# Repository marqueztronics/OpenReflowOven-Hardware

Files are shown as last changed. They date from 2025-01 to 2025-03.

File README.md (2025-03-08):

OpenReflowOven_Logo

# Open Reflow Oven

A reflow oven controller to be used with regular electric toaster ovens.

This is the repository for the PCB design files.

PCB designed in Altium CircuitStudio.

Current status: Finished v1.0 PCB layout. Tested with some basic reflows.

Note: If you are looking for schematics, Gerber, BOM, etc. they are under the "Default Configuration" folder. Circuit Studio has a weird directory structure.

[Firmware repo](https://github.com/marqueztronics/OpenReflowOven-Firmware)

# Video
Open Reflow Oven Demo (https://www.youtube.com/watch?v=Xi4_opGDsho)

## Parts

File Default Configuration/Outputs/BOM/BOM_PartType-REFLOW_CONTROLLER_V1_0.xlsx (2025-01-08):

Designator | Quantity | Description | Manufacturer | Manufacturer Part Number | Price Unit | Price 1K | Supplier 1 | Supplier Part Number 1
BZ1 | 1 | 60dB Externally Driven Externally Driven 4kHz Plugin,D=12.2mm Buzzers ROHS | TDK | PS1240P02CT3 | 0.2373 | 0.1495 | LCSC | C76873
C1, C3 | 2 | 50V 10nF X7R ±10% 0603 Multilayer Ceramic Capacitors MLCC - SMD/SMT ROHS | Samsung Electro-Mechanics | CL10B103KB8NNNC | 0.0028 | 0.0022 | LCSC | C1589
C2, C4, C11, C15, C16, C17, C18, C21 | 8 | 50V 100nF X7R ±10% 0603 Multilayer Ceramic Capacitors MLCC - SMD/SMT ROHS | Samsung Electro-Mechanics | CL10B104KB8NNNC | 0.0024 | 0.0019 | LCSC | C1591
C5 | 1 | 1000uF 16V 78mO@100kHz ±20% 1.05A@100kHz Plugin,D10xL20mm Aluminum Electrolytic Capacitors - Leaded ROHS | Rubycon | 16YXF1000MEFC10X20 | 0.1397 | 0.0774 | LCSC | C110138
C6, C9 | 2 | 35V 2.2uF X7R ±10% 0805 Multilayer Ceramic Capacitors MLCC - SMD/SMT ROHS | TDK | CGA4J1X7R1V225KT0Y0E | 0.1161 | 0.0724 | LCSC | C342739
C7 | 1 | 50V 68pF NP0 ±5% 0603 Multilayer Ceramic Capacitors MLCC - SMD/SMT ROHS | Yageo | CC0603JRNPO9BN680 | 0.0027 | 0.0021 | LCSC | C62782
C8, C19, C22 | 3 | 16V 1uF X7R ±10% 0603 Multilayer Ceramic Capacitors MLCC - SMD/SMT ROHS | Samsung Electro-Mechanics | CL10B105KO8NNNC | 0.0033 | 0.0029 | LCSC | C59782
C10 | 1 | 16V 47uF X5R ±10% 1210 Multilayer Ceramic Capacitors MLCC - SMD/SMT ROHS | Murata | GRM32ER61C476KE15L | 0.1302 | 0.079 | LCSC | C77101
C14, C20 | 2 | 16V 4.7uF X7R ±10% 0805 Multilayer Ceramic Capacitors MLCC - SMD/SMT ROHS | Taiyo Yuden | EMK212B7475KG-T | 0.0182 | 0.0145 | LCSC | C92762
D1, D2 | 2 | Single 3.32V~3.53V 400mW 3.3V SOD-323 Zener Diodes ROHS | Nexperia | PDZ3.3B,115 | 0.0192 | 0.013 | LCSC | C426855
D3 | 1 | 35A 1V@400mA 800mA 600V MBS Bridge Rectifiers ROHS | Micro Commercial Components | MB6S-TP | 0.0398 | 0.0284 | LCSC | C85619
D4 | 1 | 1A 1kV 1.1V@1A SMA(DO-214AC) Diodes - General Purpose ROHS | Micro Commercial Components | M7-TP | 0.013 | 0.0104 | LCSC | C85148
FB1 | 1 | 50mO ±25% 120O@100MHz 0603 Ferrite Beads ROHS | Murata Electronics | BLM18PG121SN1D | 0.0062 | 0.0049 | LCSC | C14709
FH1, FH2 | 2 | Circuit Board Mount Fuse Clips for 5mm Diameter Fuses | Littelfuse | 01000020Z | 0.206 | 0.1324 | LCSC | C142797
J1, J8 | 2 | 1x2P 2P XH 1 2.5mm 2 Brass Plugin,P=2.5mm Wire To Board Connector ROHS | JST | B2B-XH-A(LF)(SN) | 0.0301 | 0.0208 | LCSC | C158012
J2, J3 | 2 | 1x2P 2P VH 1 7.92mm 2 Brass Plugin,P=7.92mm Wire To Board Connector ROHS | JST | B2P3-VH(LF)(SN) | 0.0558 | 0.0310 | LCSC | C160745
J4 | 1 | C14 Right Angle Panel Mount, PCB Mount IEC Connector Male, 10A, 250 V | Bulgin | PX0580/PC/12132 | 5.03 | 4.37 | RS | 261-5840
J5 | 1 | C13 Right Angle Panel Mount, PCB Mount IEC Connector Socket, 10A, 250 V | Bulgin | PX0675/PC | 6.49 | 5.45 | RS | 801-948
J6 | 1 | 14P 2.54mm Single Row 1x14P Plugin,P=2.54mm Pin Headers ROHS | MINTRON | MTP125-1114S1 | 0.0696 | 0.0435 | LCSC | C5142340
J7 | 1 | -20?~+90? 2mm Card Slot MicroSD card (TF card) Self-bouncing SMD SD Card / Memory Card Connector ROHS | SHOU HAN | TF PUSH | 0.0465 | 0.03 | LCSC | C393941
L1 | 1 | 860mA 39uH ±20% SMD,6.7x6.7mm Power Inductors ROHS | Abracon | ASPI-0602S-390M-T | 0.0798 | 0.0437 | LCSC | C187310
Q1, Q2, Q3 | 3 | 40V 250mW 200mA NPN SOT-23 Bipolar Transistors - BJT ROHS | Nexperia | MMBT3904 | 0.0155 | 0.0124 | LCSC | C108429
R1, R5, R11, R18 | 4 | 100mW Thick Film Resistors 75V ±100ppm/? ±1% 100kO 0603 Chip Resistor - Surface Mount ROHS | Yageo | RC0603FR-07100KL | 0.0009 | 0.0007 | LCSC | C14675
R2, R3, R16, R17, R20, R21, R22, R26 | 8 | 100mW Thick Film Resistors 75V ±100ppm/? ±1% 1kO 0603 Chip Resistor - Surface Mount ROHS | Yageo | RC0603FR-071KL | 0.001 | 0.0008 | LCSC | C22548
R4, R12 | 2 | 100mW Thick Film Resistors 75V ±100ppm/? ±1% 100O 0603 Chip Resistor - Surface Mount ROHS | Yageo | RC0603FR-07100RL | 0.001 | 0.0007 | LCSC | C105588
R6, R14 | 2 | 100mW Thick Film Resistors 75V ±100ppm/? ±1% 10kO 0603 Chip Resistor - Surface Mount ROHS | Yageo | RC0603FR-0710KL | 0.0009 | 0.0007 | LCSC | C98220
R7, R15 | 2 | 100mW Thick Film Resistors 75V ±100ppm/? ±1% 4.7kO 0603 Chip Resistor - Surface Mount ROHS | Yageo | RC0603FR-074K7L | 0.001 | 0.0008 | LCSC | C99782
R8, R10 | 2 | 100mW Thick Film Resistors 75V ±100ppm/? ±1% 2.2kO 0603 Chip Resistor - Surface Mount ROHS | Yageo | RC0603FR-072K2L | 0.0011 | 0.0009 | LCSC | C114662
R9 | 1 | 100mW Thick Film Resistors 75V ±100ppm/? ±1% 1.5kO 0603 Chip Resistor - Surface Mount ROHS | Yageo | RC0603FR-071K5L | 0.0012 | 0.0009 | LCSC | C114668
R13 | 1 | 100mW Thick Film Resistors 75V ±100ppm/? ±1% 8.45kO 0603 Chip Resistor - Surface Mount ROHS | Yageo | RC0603FR-078K45L | 0.0012 | 0.001 | LCSC | C163417
R19 | 1 | 100mW Thick Film Resistors 75V ±100ppm/? ±1% 13.7kO 0603 Chip Resistor - Surface Mount ROHS | Yageo | RC0603FR-0713K7L | 0.0013 | 0.001 | LCSC | C482771
RT1 | 1 | 10kO 330uA 100mW ±1% 3950K ±1% 0603 NTC Thermistors ROHS | Sunlord | SDNT1608X103F3950FTF | 0.0206 | 0.0148 | LCSC | C279936
RV1 | 1 | VARISTOR 470V 1.2KA DISC 7MM | Bourns | MOV-07D471K | 0.0857 | 0.0532 | LCSC | C1527385
T1 | 1 | Block 9V ac 1 Output Through Hole PCB Transformer, 3.2VA | Block | VB 3,2/1/9 | 7.24 | 7.24 | RS | 732-0398
U1 | 1 | 17MHz 0.1pA Dual VSSOP-8 Precision OpAmps ROHS | Texas Instruments | LMP7716MM/NOPB | 2.1951 | 1.3767 | LCSC | C72531
U2 | 1 | 5pA Single 1MHz SOT-23-5 Operational Amplifier ROHS | Texas Instruments | TLV9001IDBVR | 0.2141 | 0.136 | LCSC | C398363
U3 | 1 | 4.5-V to 28-V Input, 2-A Output, EMI Friendly Synchronous Step Down Converter | Texas Instruments | TPS54202DDCR | 0.1566 | 0.0922 | LCSC | C191884
U4 | 1 | 300mA 75dB@(100Hz) Fixed 3.3V Positive electrode 13.2V SOT-23 Linear Voltage Regulators (LDO) ROHS | Diodes Incorporated | AP2210N-3.3TRG1 | 0.0907 | 0.0597 | LCSC | C155508
U5 | 1 | 512KB 1.7V~3.6V ARM-M4 128KB 180MHz FLASH 50 LQFP-64(10x10) Microcontrollers (MCU/MPU/SOC) ROHS | STMicroelectronics | STM32F446RET6 | 3.3018 | 2.3276 | LCSC | C69336

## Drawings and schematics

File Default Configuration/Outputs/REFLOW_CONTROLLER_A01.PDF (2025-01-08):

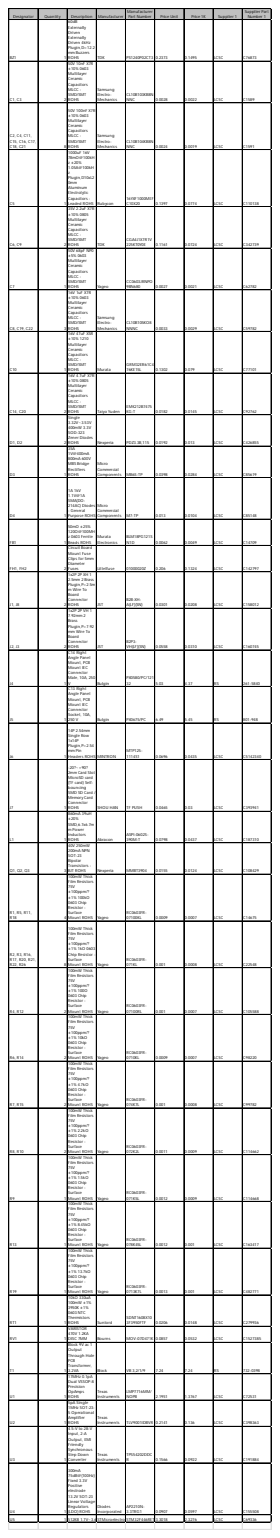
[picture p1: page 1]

BZ1 | | 60dB Externally Driven Externally Driven 4kHz Plugin,D=12.2 mm Buzzers 1 ROHS | TDK | PS1240P02CT3 | 0.2373 | 0.1495 | LCSC | C76873

Designator | Quantity | Description | Manufacturer | Manufacturer Part Number | Price Unit | Price 1K | Supplier 1 | Supplier Part Number 1

C1, C3 | | 50V 10nF X7R ±10% 0603 Multilayer Ceramic Capacitors MLCC -2 SMD/SMT ROHS | Samsung Electro-Mechanics | CL10B103KB8N NNC | 0.0028 | 0.0022 | LCSC | C1589

C2, C4, C11, C15, C16, C17, C18, C21 | | 50V 100nF X7R ±10% 0603 Multilayer Ceramic Capacitors MLCC -8 SMD/SMT ROHS | Samsung Electro-Mechanics | CL10B104KB8N NNC | 0.0024 | 0.0019 | LCSC | C1591

C5 | | 1000uF 16V 78mO@100kH z ±20% 1.05A@100kH z Plugin,D10xL2 0mm Aluminum Electrolytic Capacitors -1 Leaded ROHS | Rubycon | 16YXF1000MEF C10X20 | 0.1397 | 0.0774 | LCSC | C110138

C6, C9 | | 35V 2.2uF X7R ±10% 0805 Multilayer Ceramic Capacitors MLCC -SMD/SMT 2 ROHS | TDK | CGA4J1X7R1V 225KT0Y0E | 0.1161 | 0.0724 | LCSC | C342739

C7 | | 50V 68pF NP0 ±5% 0603 Multilayer Ceramic Capacitors MLCC -SMD/SMT 1 ROHS | Yageo | CC0603JRNPO 9BN680 | 0.0027 | 0.0021 | LCSC | C62782

C8, C19, C22 | | 16V 1uF X7R ±10% 0603 Multilayer Ceramic Capacitors MLCC -3 SMD/SMT ROHS | Samsung Electro-Mechanics | CL10B105KO8 NNNC | 0.0033 | 0.0029 | LCSC | C59782

C10 | | 16V 47uF X5R ±10% 1210 Multilayer Ceramic Capacitors MLCC -SMD/SMT 1 ROHS | Murata | GRM32ER61C4 76KE15L | 0.1302 | 0.079 | LCSC | C77101

C14, C20 | | 16V 4.7uF X7R ±10% 0805 Multilayer Ceramic Capacitors MLCC -2 SMD/SMT ROHS | Taiyo Yuden | EMK212B7475 KG-T | 0.0182 | 0.0145 | LCSC | C92762

D1, D2 | | Single 3.32V~3.53V 400mW 3.3V SOD-323 Zener Diodes 2 ROHS | Nexperia | PDZ3.3B,115 | 0.0192 | 0.013 | LCSC | C426855

D3 | | 35A 1V@400mA 800mA 600V MBS Bridge Rectifiers 1 ROHS | Micro Commercial Components | MB6S-TP | 0.0398 | 0.0284 | LCSC | C85619

D4 | | 1A 1kV 1.1V@1A SMA(DO-214AC) Diodes 1 - General Purpose ROHS | Micro Commercial Components | M7-TP | 0.013 | 0.0104 | LCSC | C85148

FB1 | | 50mO ±25% 120O@100MH z 0603 Ferrite 1 Beads ROHS | Murata Electronics | BLM18PG121S N1D | 0.0062 | 0.0049 | LCSC | C14709

FH1, FH2 | | Circuit Board Mount Fuse Clips for 5mm 2 Diameter Fuses | Littelfuse | 01000020Z | 0.206 | 0.1324 | LCSC | C142797

J1, J8 | | 1x2P 2P XH 1 2.5mm 2 Brass Plugin,P=2.5m m Wire To Board Connector 2 ROHS | JST | B2B-XH-A(LF)(SN) | 0.0301 | 0.0208 | LCSC | C158012

J2, J3 | | 1x2P 2P VH 1 7.92mm 2 Brass Plugin,P=7.92 mm Wire To Board Connector 2 ROHS | JST | B2P3-VH(LF)(SN) | 0.0558 | 0.0310 | LCSC | C160745

J4 | | C14 Right Angle Panel Mount, PCB Mount IEC Connector 1 Male, 10A, 250 V | Bulgin | PX0580/PC/121 32 | 5.03 | 4.37 | RS | 261-5840

J5 | | C13 Right Angle Panel Mount, PCB Mount IEC Connector Socket, 10A, 1 250 V | Bulgin | PX0675/PC | 6.49 | 5.45 | RS | 801-948

J6 | | 14P 2.54mm Single Row 1x14P Plugin,P=2.54 mm Pin 1 Headers ROHS | MINTRON | MTP125-1114S1 | 0.0696 | 0.0435 | LCSC | C5142340

J7 | | -20?~+90? 2mm Card Slot MicroSD card (TF card) Self-bouncing SMD SD Card Memory Card Connector 1 ROHS | / SHOU HAN | TF PUSH | 0.0465 | 0.03 | LCSC | C393941

L1 | | 860mA 39uH ±20% SMD,6.7x6.7m m Power Inductors 1 ROHS | Abracon | ASPI-0602S-390M-T | 0.0798 | 0.0437 | LCSC | C187310

Q1, Q2, Q3 | | 40V 250mW 200mA NPN SOT-23 Bipolar Transistors -3 BJT ROHS | Nexperia | MMBT3904 | 0.0155 | 0.0124 | LCSC | C108429

R1, R5, R11, R18 | | 100mW Thick Film Resistors 75V ±100ppm/? ±1% 100kO 0603 Chip Resistor -4 Surface Mount ROHS | Yageo | RC0603FR-07100KL | 0.0009 | 0.0007 | LCSC | C14675

R2, R3, R16, R17, R20, R21, R22, R26 | | 100mW Thick Film Resistors 75V ±100ppm/? ±1% 1kO 0603 Chip Resistor -8 Surface Mount ROHS | Yageo | RC0603FR-071KL | 0.001 | 0.0008 | LCSC | C22548

R4, R12 | | 100mW Thick Film Resistors 75V ±100ppm/? ±1% 100O 0603 Chip Resistor -Surface 2 Mount ROHS | Yageo | RC0603FR-07100RL | 0.001 | 0.0007 | LCSC | C105588

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

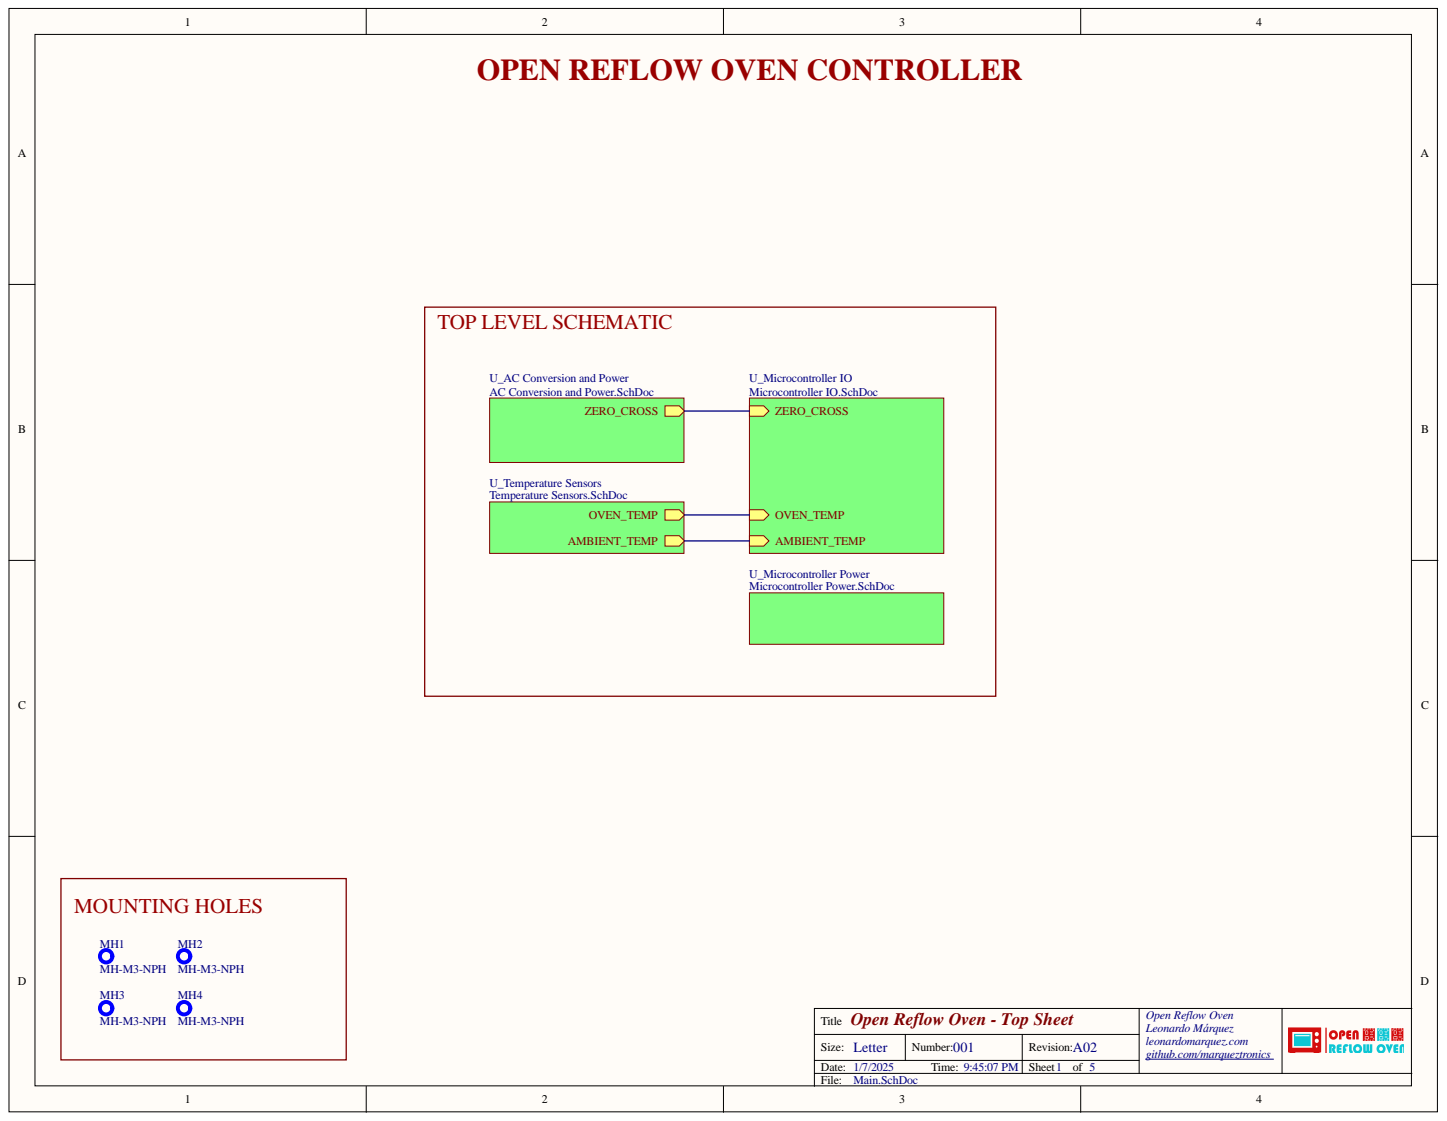
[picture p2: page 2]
U_Microcontroller IO Microcontroller IO.SchDoc; MOUNTING HOLES

OPEN REFLOW OVEN CONTROLLER

TOP LEVEL SCHEMATIC

U_AC Conversion and Power
AC Conversion and Power.SchDoc

U_Temperature Sensors
Temperature Sensors.SchDoc

U_Microcontroller Power
Microcontroller Power.SchDoc

Open Reflow Oven - Top Sheet Title | Open Reflow Oven Leonardo Márquez leonardomarquez.com github.com/marqueztronics

Size: Letter | Number: 001 | Revision: A02
Date: 1/7/2025 Time: 9:45:07 PM | | Sheet of

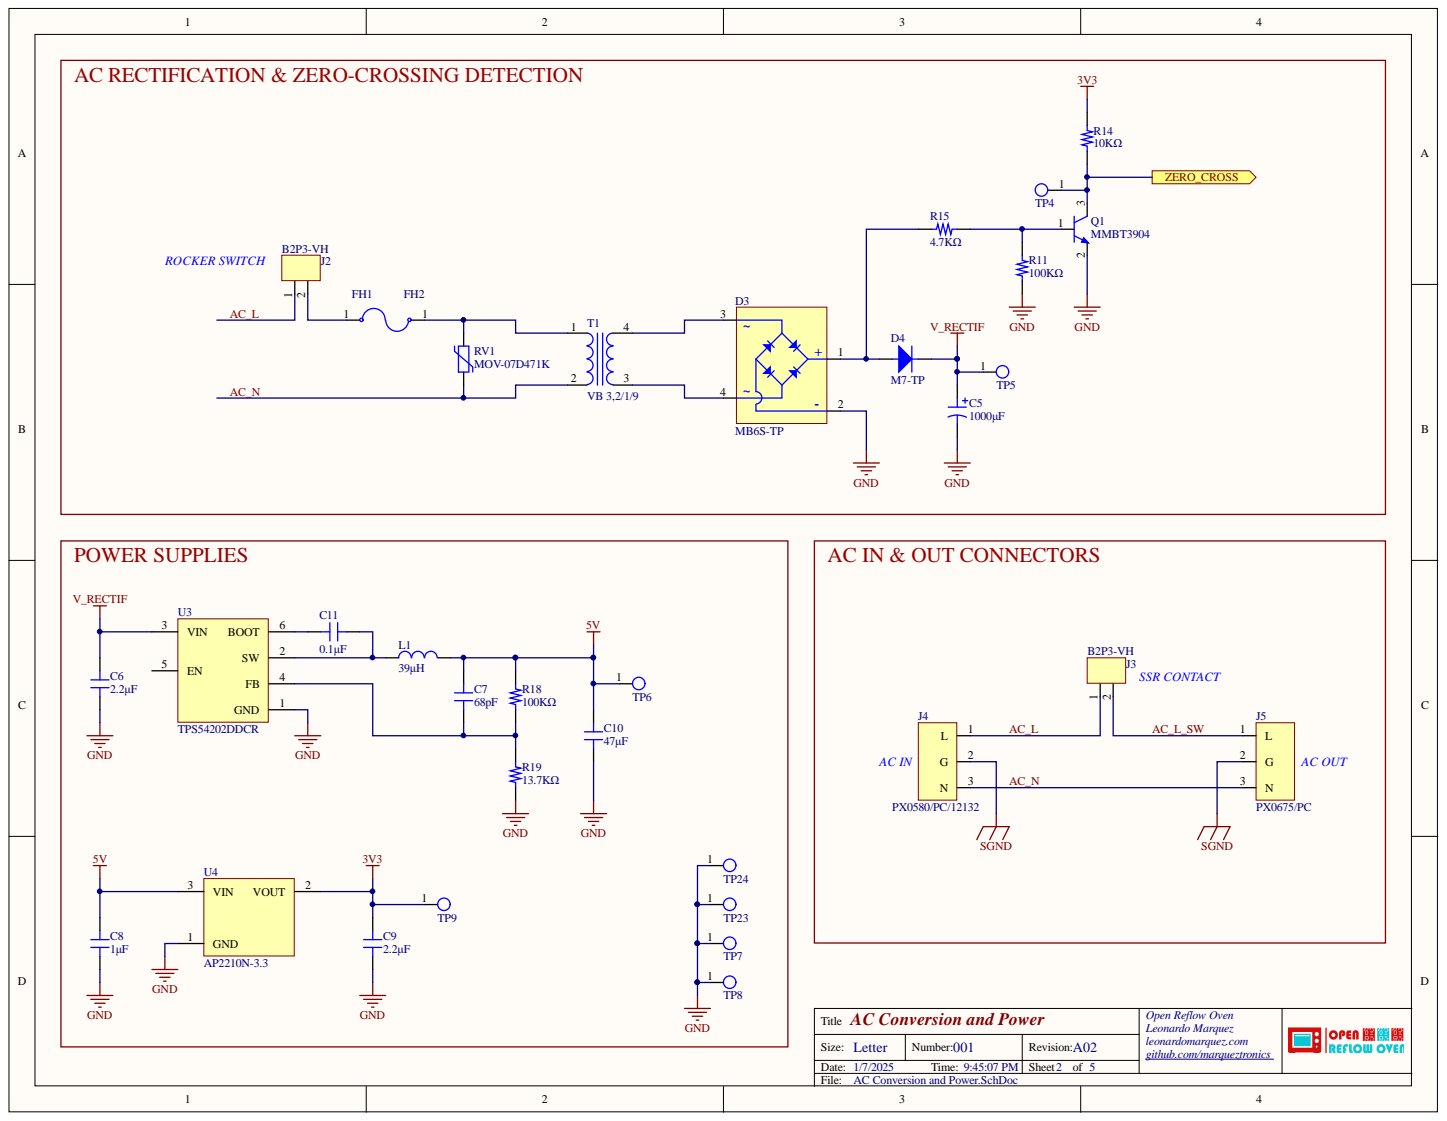
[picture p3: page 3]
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

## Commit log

2024-05-08 Added display, buttons and modified power circuitry
    [AC Conversion and Power.SchDoc, Microcontroller IO.SchDoc, Microcontroller Power.SchDoc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]
2024-05-08 Remove AC Zero-Crossing Detection.SchDoc
    [AC Zero-Crossing Detection.SchDoc]
2024-05-10 Added Display, buttons, relay connectors, AC protections, and more...
    [AC Conversion and Power.SchDoc, Main.SchDoc, Microcontroller IO.SchDoc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]
2024-05-16 Finished Routing and added logos to silkscreen
    [AC Conversion and Power.SchDoc, Main.SchDoc, Microcontroller IO.SchDoc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]
2024-05-18 Final modifications for v0.1, generated fab outputs
    [BOM_PartType-REFLOW_CONTROLLER_A01.xlsx, Pick Place for REFLOW_CONTROLLER_A01.csv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]
2024-05-22 Add LEDs for Power and status indication, generate new outputs with these changes
    [AC Conversion and Power.SchDoc, BOM_PartType-REFLOW_CONTROLLER_A01.xlsx, Microcontroller IO.SchDoc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]
2024-09-23 Start of v1.0
    [AC Conversion and Power.SchDoc, BOM_PartType-REFLOW_CONTROLLER_A01.xls, BOM_PartType-REFLOW_CONTROLLER_A01.xlsx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]
2024-10-15 Finish PCB layout and generate outputs
    [AC Conversion and Power.SchDoc, BOM_PartType-REFLOW_CONTROLLER_A01.xls, BOM_PartType-REFLOW_CONTROLLER_V1_0.xlsx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]
2025-01-08 Fixed IEC connectors mechanics, moved SD Card slot position
    [BOM_PartType-REFLOW_CONTROLLER_V1_0.xlsx, Microcontroller IO.SchDoc, REFLOW_CONTROLLER.SchLib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]
2025-01-08 Update Output files
    [BOM_PartType-REFLOW_CONTROLLER_V1_0.xlsx, Pick Place for REFLOW_CONTROLLER_V1_0.csv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]
2025-03-08 Update project file
    [REFLOW_CONTROLLER_V1_0.PrjPcb]
